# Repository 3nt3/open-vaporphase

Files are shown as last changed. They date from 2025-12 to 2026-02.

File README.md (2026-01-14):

# Open Vaporphase

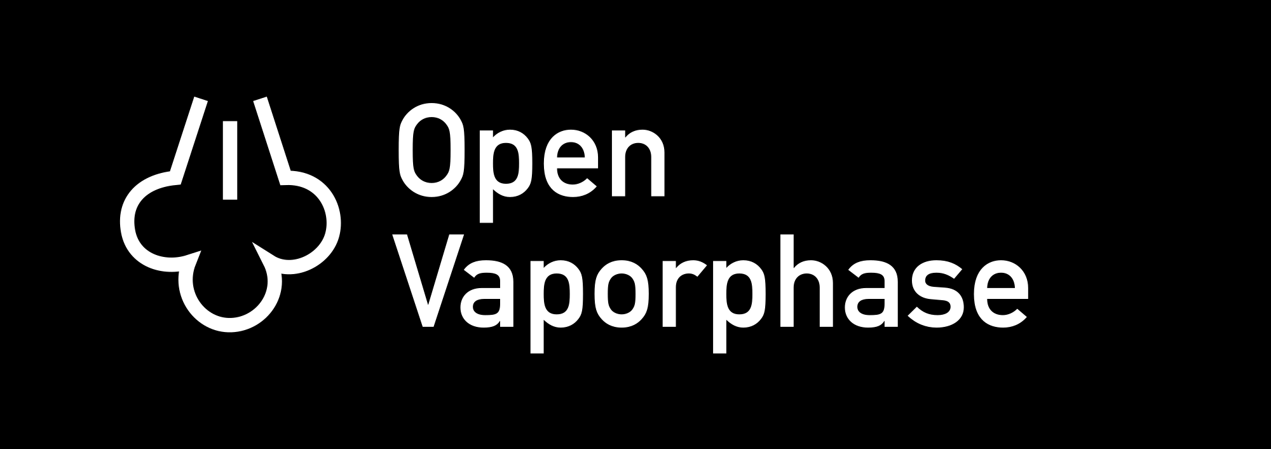
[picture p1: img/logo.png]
Open Vaporphase Logo


# Hardware

## Requirements

- Active cooling
- Ventilation
- Lid switch
- Buzzer to play the Forelle song like a samsung washing machine (required to be configurable to also imitate a rice cooker)

## Safety

We try to follow relevant EU legislature Directive 2006/42/EC (Machinery Directive) as a source of best practices.

### Hazards

- Thermal: High-temperature fluids and surfaces
- Chemical: Vapor phase fluids (PFPE, Galden, etc.)
- Electrical

### Ideas

- Heater control fails OFF
- Loss of sensor input disables heating
- Prevention of runoff heating when liquid is missing
- Lid-open condition prevents heating
- Manual emergency stop immediately removes power

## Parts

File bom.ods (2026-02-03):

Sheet: Sheet1
Open Vaporphase BOM
Qty | Description | Supplier | Part Number | Individual Cost | Total Cost | Note | Kilometerstein | Status
4.00 | TT-PT1000B-2050-11-AUNITEWA TEMPERATURE SENSORS-Sensor Temperatur | TME | TT-PT1000B-2050-11 | 2.78 € | 11.12 € |  | 1.00 | To-Do
2.00 | RS PRO Heizelement Heizpatrone 500 W / 220 V ac, Ø 16 mm, Länge 150mm | RS-Components | 860-6993 | 32.45 € | 64.90 € |  | 1.00 | To-Do
1.00 | TE Connectivity Mini Puck SSRMP Tafelmontage Halbleiterrelais mit Nulldurchgang, 1-poliger Schließer 280 V / 25 A | RS-Components | 204-7642 | 18.04 € | 18.04 € |  | 1.00 | To-Do
1.00 | RS PRO DIN-Schienen Netzteil Schaltnetzteile 5V dc / 2.4A 12W 90 → 264V ac | RS-Components | 225-9899 | 16.27 € | 16.27 € |  | 2.00 | To-Do
1.00 | 30×30 Bosch Rexroth compatible aluminium extrusion and connectors | Motedis |  | 60.00 € | 60.00 € | TODO: actual itemized list | 2.00 | To-Do
1.00 | METRO Professional GN-Behälter 1/3, 200 mm, Edelstahl 18/10 | Metro | AAA0046067392 | 16.65 € | 16.65 € |  | 1.00 | Done
1.00 | Custom Machined Heatsink | JLCCNC |  | 45.00 € | 45.00 € |  | 1.00 | Ordered
1.00 | Cooper Pipe Ø 15 mm, l = 2000 mm | Bauhaus | 27689806 | 21.00 € | 21.00 € |  | 1.00 | To-Do
2.00 | Flow sensors | Amazon | https://www.amazon.de/ARCELI-Wasserdurchfluss-Wassersteuerung-Wasserdurchflussschalter-Durchflussmesser/dp/B07MY24YFX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 | 8.00 € | 16.00 € | Can’t find any affordable ones from reputable suppliers | 2.00 | To-Do
1.00 | 480×320px IPS Display with ILI9486 controller | Amazon | https://www.amazon.de/Binghe-5-Zoll-TFT-Farbmodul-SD-Kartensockel-Reichhaltige-Kompatibel/dp/B0DS1QDDK1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 | 17.00 € | 17.00 € |  | 1.00 | To-Do
1.00 | ESP32-S3-WROOM-1-N16 | Digikey |  |  | 0.00 € | Lol | 1.00 | To-Do
1.00 | Misc | Digikey |  |  | 0.00 € |  | 1.00 | To-Do
1.00 | High Temperature Silicone RUBAAAAH: TFC Trollfactory Silkon Kautschunk Typ 3 | Trollfactory | https://trollfactory.de/Produkte/Silikon-Kautschuk/Verarbeitungszeit/sehr-schnell-5-Min/TFC4020/TFC-Troll-Factory-Silikon-Kautschuk-Typ-3-HB-Zinnguss-hitzebes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 | 19.90 € | 19.90 € |  | 1.00 | To-Do
1.00 | Copper Sheet Metal 2 mm | ProKilo | N/A | 20.00 € | 20.00 € |  | 1.00 | To-Do
1.00 | Glass plate | ??? | ??? | ??? | #VALUE! |  | 1.00 | To-Do
1.00 | Nutri Score: LUFT |  |  | 40.00 € | 40.00 € |  | 2.00 | To-Do
1.00 | Galdne |  |  | 80.00 | 80.00 € |  | 1.60 | To-Do
1.00 | Aluminium Barstock 30×5 | ProKilo | N/A | 7.70 € | 7.70 € |  | 1.00 | To-Do
 |  |  |  | Total v0.1 | 241.31 €
 |  |  |  | Total Cost | 453.58 €

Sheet: Sheet2
Qty | Description | Supplier | Part Number | Individual Cost | Total Cost | Note | Kilometerstein | Status
4.00 | RS PRO PT100 Chip RTD-Sensor Platin Ø 2mm x 5mm, -50°C → +500°C | RS-Components | 611-7801 | 4.13 € | 16.52 € |  | 1.00 | Done
2.00 | RS PRO Heizelement Heizpatrone 500 W / 220 V ac, Ø 16 mm, Länge 150mm | RS-Components | 860-6993 | 32.45 € | 64.90 € |  | 1.00 | Done
1.00 | TE Connectivity Mini Puck SSRMP Tafelmontage Halbleiterrelais mit Nulldurchgang, 1-poliger Schließer 280 V / 25 A | RS-Components | 204-7642 | 18.04 € | 18.04 € |  | 1.00 | Done
1.00 | RS PRO DIN-Schienen Netzteil Schaltnetzteile 5V dc / 2.4A 12W 90 → 264V ac | RS-Components | 225-9899 | 16.27 € | 16.27 € |  | 2.00 | To-Do
1.00 | 30×30 Bosch Rexroth compatible aluminium extrusion and connectors | Motedis |  | 60.00 € | 60.00 € | TODO: actual itemized list | 2.00 | To-Do
1.00 | METRO Professional GN-Behälter 1/3, 200 mm, Edelstahl 18/10 | Metro | AAA0046067392 | 16.65 € | 16.65 € |  | 1.00 | Done
1.00 | Custom Machined Heatsink | JLCCNC |  | 45.00 € | 45.00 € |  | 1.00 | Ordered
1.00 | Cooper Pipe Ø 15 mm, l = 2000 mm | Bauhaus | 27689806 | 21.00 € | 21.00 € |  | 1.00 | To-Do
2.00 | Flow sensors | Amazon | https://www.amazon.de/ARCELI-Wasserdurchfluss-Wassersteuerung-Wasserdurchflussschalter-Durchflussmesser/dp/B07MY24YFX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 | 8.00 € | 16.00 € | Can’t find any affordable ones from reputable suppliers | 2.00 | To-Do
1.00 | 480×320px IPS Display with ILI9486 controller | Amazon | https://www.amazon.de/Binghe-5-Zoll-TFT-Farbmodul-SD-Kartensockel-Reichhaltige-Kompatibel/dp/B0DS1QDDK1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 | 17.00 € | 17.00 € |  | 1.00 | To-Do
1.00 | ESP32-S3-WROOM-1-N16 | Digikey |  |  | 0.00 € | Lol | 1.00 | To-Do
1.00 | Misc | Digikey |  |  | 0.00 € |  | 1.00 | To-Do
1.00 | High Temperature Silicone RUBAAAAH: TFC Trollfactory Silkon Kautschunk Typ 3 | Trollfactory | https://trollfactory.de/Produkte/Silikon-Kautschuk/Verarbeitungszeit/sehr-schnell-5-Min/TFC4020/TFC-Troll-Factory-Silikon-Kautschuk-Typ-3-HB-Zinnguss-hitzebes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 | 19.90 € | 19.90 € |  | 1.00 | To-Do
1.00 | Copper Sheet Metal 2 mm | ProKilo | N/A | 20.00 € | 20.00 € |  | 1.00 | To-Do
1.00 | Glass plate | ??? | ??? | ??? | #VALUE! |  | 1.00 | To-Do
1.00 | Nutri Score: LUFT |  |  | 40.00 € | 40.00 € |  | 2.00 | To-Do
1.00 | Galdne |  |  | 80.00 | 80.00 € |  | 1.60 | To-Do
1.00 | Aluminium Barstock 30×5 | ProKilo | N/A | 7.70 € | 7.70 € |  | 1.00 | To-Do

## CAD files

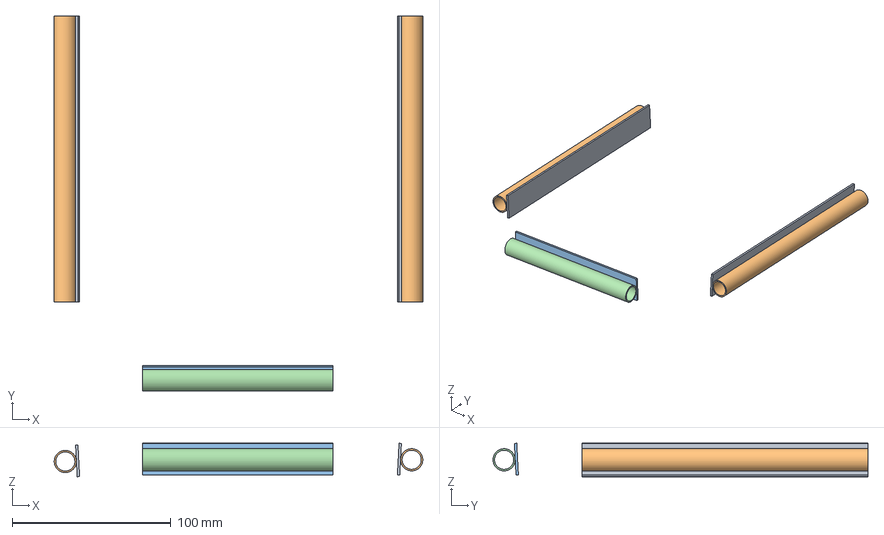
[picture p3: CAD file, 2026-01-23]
cad/open-vaporphase.FCStd
232.0 x 236.0 x 21.1 mm
spreader x 2
pipe x 2
spreader001
pipe001

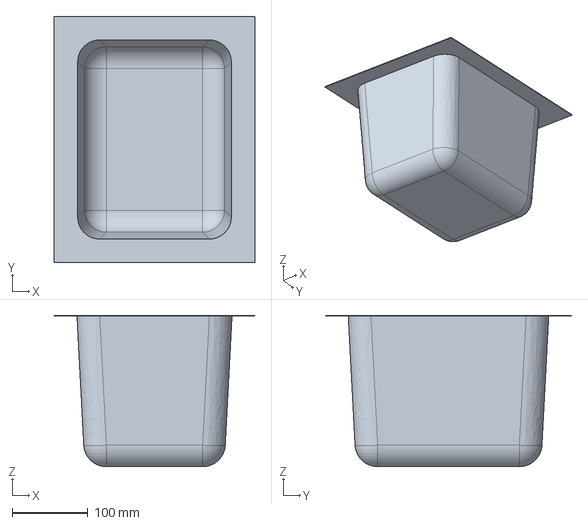
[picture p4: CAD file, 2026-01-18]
cad/res/1-2 gastronorm.FCStd
265.0 x 325.0 x 200.0 mm

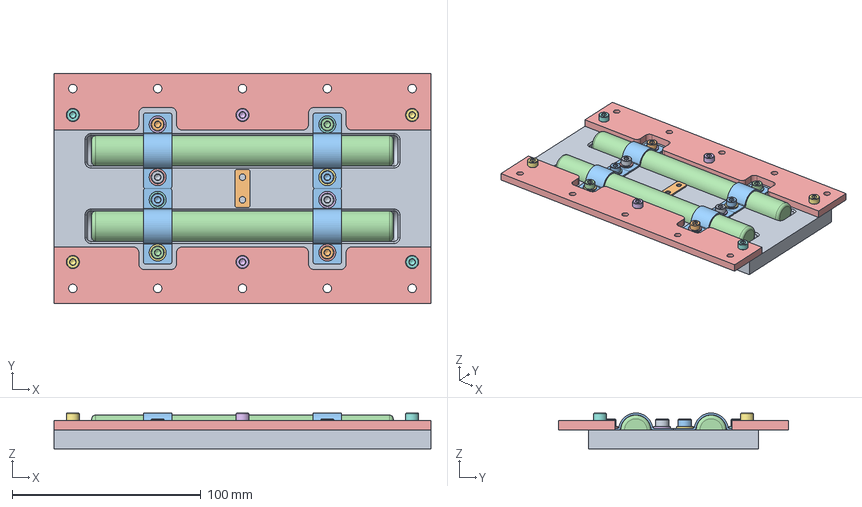
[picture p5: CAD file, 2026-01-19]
cad/16mm heater block.FCStd
200.0 x 122.0 x 19.1 mm
16mm block v2
thermocouple clamp
clamp x 4
16mm heater x 2
M4-Washer007
M4-Washer006
M4-Washer
M4-Washer001
M4x8-Screw096
M4x8-Screw095
M4x8-Screw092
M4x8-Screw
M4-Washer002
M4-Washer003
M4-Washer004
M4-Washer005
M4x8-Screw093
M4x8-Screw094
M4x8-Screw097
M4x8-Screw098
clamp thing x 2
M4x12-Screw002 x 2
M4x12-Screw x 2
M4x12-Screw003 x 2

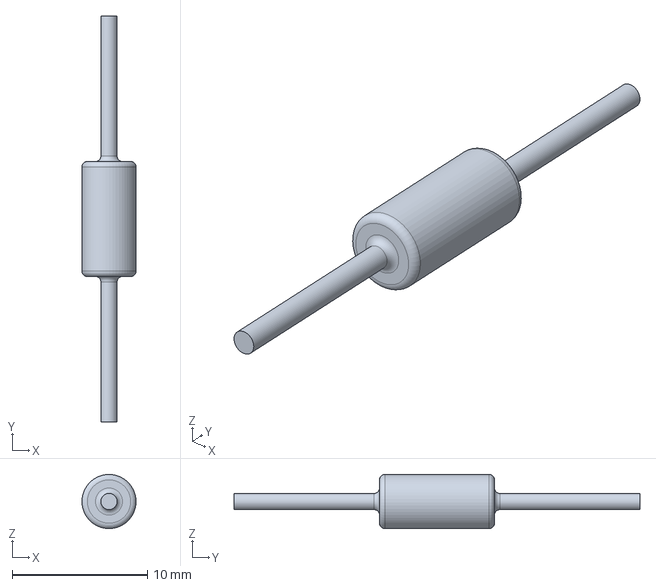
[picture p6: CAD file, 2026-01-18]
cad/res/797-6030 temperature fuse.FCStd
4.00 x 30.0 x 4.00 mm

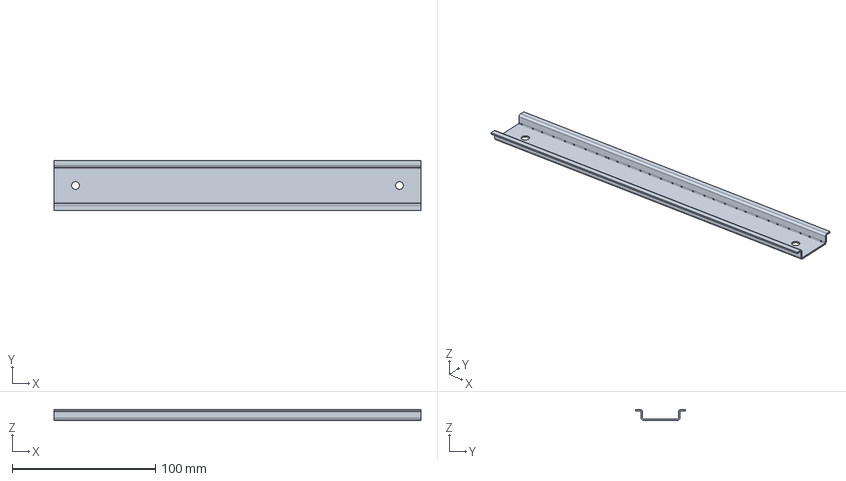
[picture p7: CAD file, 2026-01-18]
cad/res/din rail.FCStd
256.0 x 35.0 x 7.50 mm

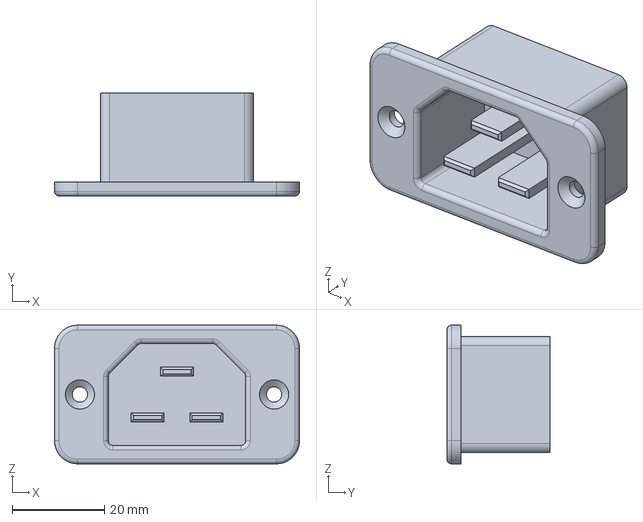
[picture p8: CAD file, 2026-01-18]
cad/res/866-2640 iec plug.FCStd
53.0 x 22.3 x 30.0 mm

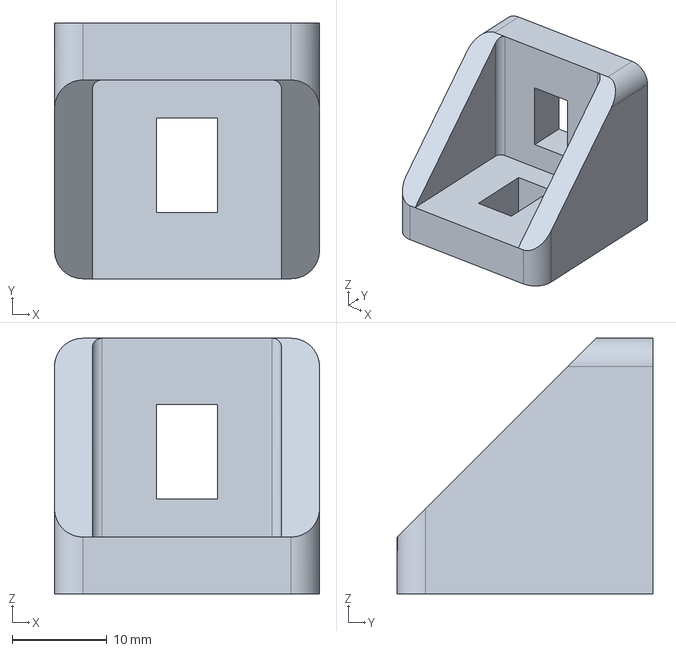
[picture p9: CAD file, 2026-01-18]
cad/res/236-7194 3030 90deg m6.FCStd
28.0 x 27.0 x 27.0 mm

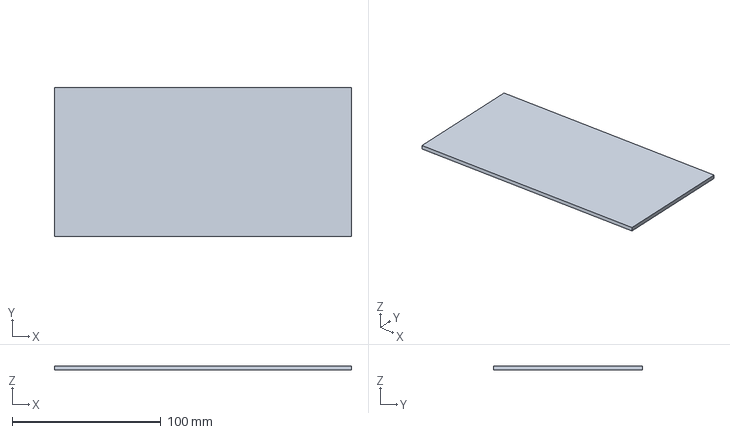
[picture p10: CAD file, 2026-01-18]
cad/res/790-4833 heating pad.FCStd
200.0 x 100.0 x 3.00 mm

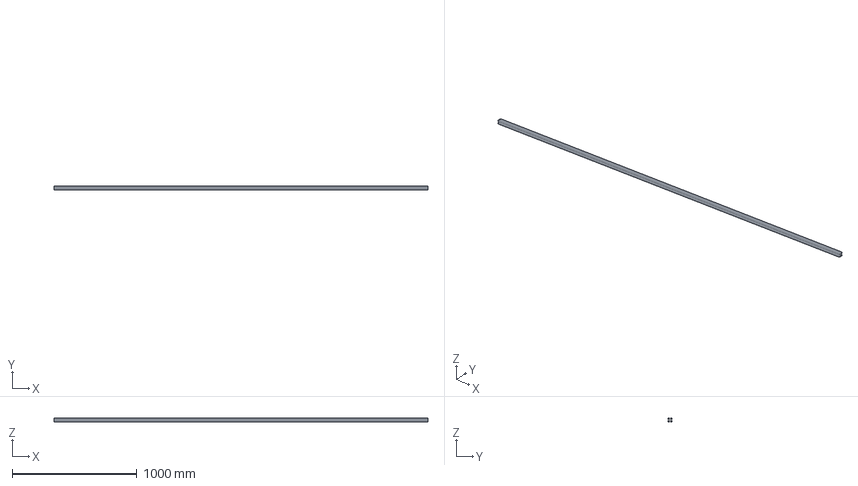
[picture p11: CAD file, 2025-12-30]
cad/res/176240558-3-3842990720_3000/3842990720_3000.stp
3000.0 x 30.0 x 30.0 mm

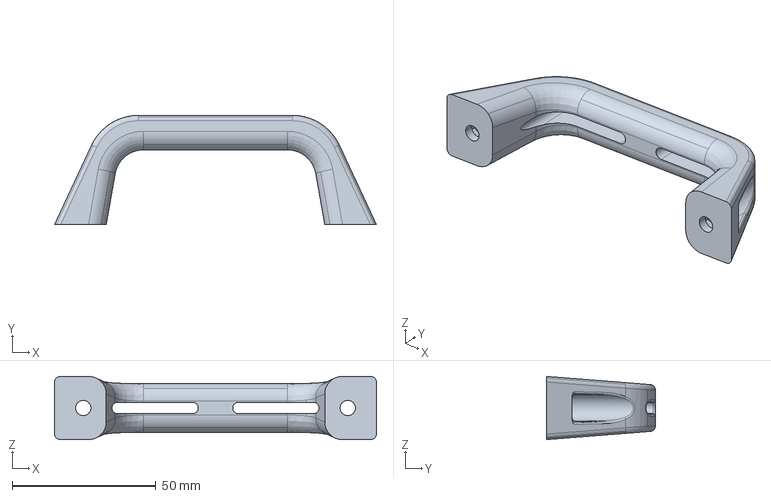
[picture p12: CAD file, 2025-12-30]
cad/res/456589.stp
112.0 x 38.0 x 22.0 mm

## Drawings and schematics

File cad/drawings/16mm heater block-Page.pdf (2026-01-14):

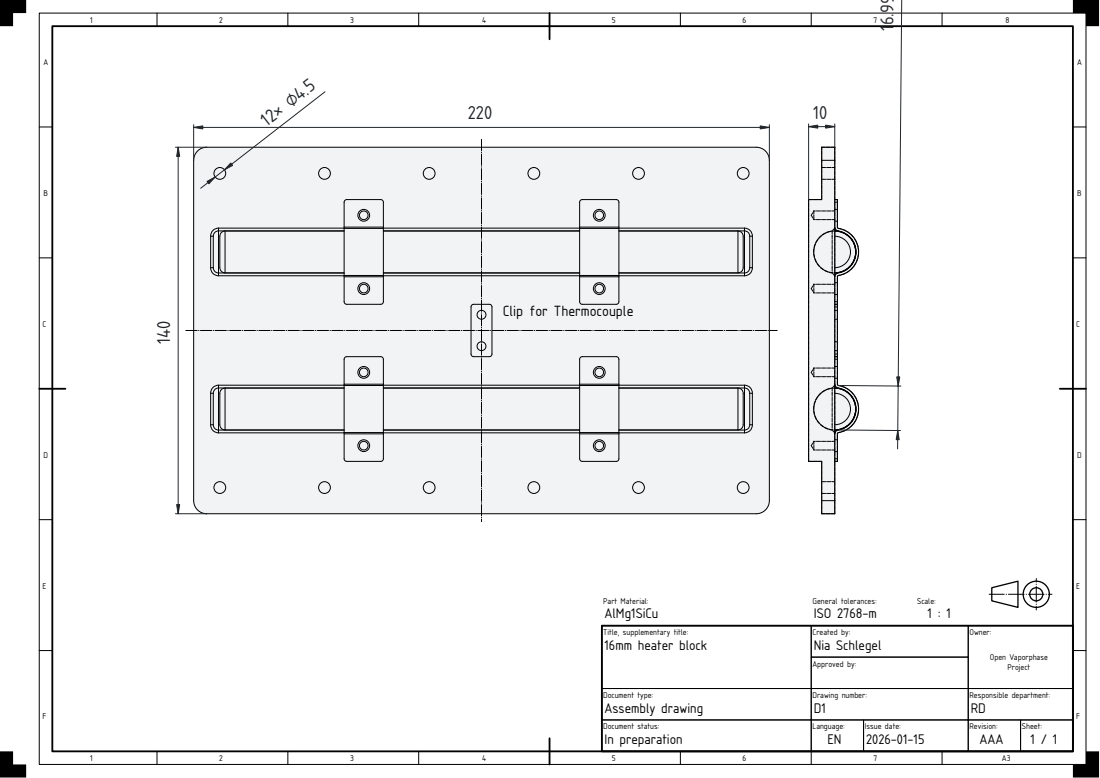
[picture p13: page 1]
Approved by:; Created by:; Part Material:; General tolerances:; Scale:; Open Vaporphase; Nia Schlegel; AlMg1SiCu; ISO 2768-m

Clip for Thermocouple

Title, supplementary title:
16mm heater block

Document type: Assembly drawing | Drawing number: D1 | Responsible department: RD

Document status: In preparation | Language: EN | Issue date: 2026-01-15 | Revision: AAA | Sheet: 1 / 1

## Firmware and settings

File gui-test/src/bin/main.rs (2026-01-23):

#![no_std]
#![no_main]
#![deny(
    clippy::mem_forget,
    reason = "mem::forget is generally not safe to do with esp_hal types, especially those \
    holding buffers for the duration of a data transfer."
)]
#![deny(clippy::large_stack_frames)]

use defmt::info;
use embassy_executor::Spawner;
use embassy_time::{Duration, Timer};
use esp_hal::clock::CpuClock;
use esp_hal::timer::timg::TimerGroup;
use {esp_backtrace as _, esp_println as _};

extern crate alloc;

// This creates a default app-descriptor required by the esp-idf bootloader.
// For more information see: <https://docs.espressif.com/projects/esp-idf/en/stable/esp32/api-reference/system/app_image_format.html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>
esp_bootloader_esp_idf::esp_app_desc!();

#[allow(
    clippy::large_stack_frames,
    reason = "it's not unusual to allocate larger buffers etc. in main"
)]
#[esp_rtos::main]
async fn main(spawner: Spawner) -> ! {
    // generator version: 1.1.0

    let config = esp_hal::Config::default().with_cpu_clock(CpuClock::max());
    let peripherals = esp_hal::init(config);

    esp_alloc::heap_allocator!(#[esp_hal::ram(reclaimed)] size: 73744);

    let timg0 = TimerGroup::new(peripherals.TIMG0);
    esp_rtos::start(timg0.timer0);

    info!("Embassy initialized!");

    let radio_init = esp_radio::init().expect("Failed to initialize Wi-Fi/BLE controller");
    let (mut _wifi_controller, _interfaces) =
        esp_radio::wifi::new(&radio_init, peripherals.WIFI, Default::default())
            .expect("Failed to initialize Wi-Fi controller");

    // TODO: Spawn some tasks
    let _ = spawner;

    loop {
        info!("Hello world!");
        Timer::after(Duration::from_secs(1)).await;
    }

    // for inspiration have a look at the examples at https://github.com/esp-rs/esp-hal/tree/esp-hal-v~1.0/examples
}

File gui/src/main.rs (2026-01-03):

use slint::{ModelRc, SharedVector, Timer, format};
use std::time::Duration;

slint::include_modules!();

fn main() {
    let main_window = MainWindow::new().unwrap();

    let cycle_duration = Duration::from_secs(15 * 60); // 15 minutes
    let start_time = std::time::Instant::now();
    let total_duration = cycle_duration;

    let mut n_past_temps = 0;
    let mut past_temperatures: [f32; 20] = [0.0; 20];

    // Update timer
    let main_window_weak = main_window.as_weak();
    let timer = Timer::default();
    timer.start(
        slint::TimerMode::Repeated,
        Duration::from_millis(100), // Update 10x per second
        move || {
            let main_window = main_window_weak.unwrap();
            let elapsed = start_time.elapsed();

            if elapsed >= total_duration {
                main_window.set_time_remaining("00:00".into());
                main_window.set_is_running(false);

                return;
            }

            let remaining = total_duration - elapsed;
            let remaining_str = format!(
                "{:02}:{:02}",
                remaining.as_secs() / 60,
                remaining.as_secs() % 60
            );

            main_window.set_time_remaining(remaining_str.into());

            // random temp between 170 and 180
            let random_temp: f32 = 170.0 + rand::random::<f32>() * 10.0;
            main_window.set_temperature(format!("{:.1}", random_temp));

            // Update past temperatures
            if n_past_temps < 20 {
                n_past_temps += 1;
            }
            past_temperatures.rotate_right(1);
            past_temperatures[0] = random_temp;

            main_window.set_past_temperatures(past_temperatures.into());
        },
    );

    main_window.run().unwrap();
}

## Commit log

2025-12-30 cad wip
    [3842990720_3000.stp, 456589.stp, 866-2640 iec plug.FCStd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]
2026-01-01 make frame more complete
    [open-vaporphase.FCStd]
2026-01-02 add temperature sensor
    [open-vaporphase.FCStd]
2026-01-02 add thermal fuse
    [open-vaporphase.FCStd]
2026-01-02 add thermal fuse cad
    [797-6030 temperature fuse.FCStd, open-vaporphase.FCStd]
2026-01-02 make frame larger to fit electrical compartment
    [open-vaporphase.FCStd]
2026-01-02 tidy cad
    [797-6030 temperature fuse.FCStd, 866-2640 iec plug.FCStd, open-vaporphase.FCStd]
2026-01-02 add din rail
    [din rail.FCStd, open-vaporphase.FCStd]
2026-01-02 add basic things to schematic
    [open-vaporphase.FCStd, open-vaporphase.kicad_pcb, open-vaporphase.kicad_sch]
2026-01-02 schematic wip
    [open-vaporphase.kicad_sch]
2026-01-03 add connectors for aluminum extrusion
    [236-7194 3030 90deg m6.FCStd, 790-4833 heating pad.FCStd, open-vaporphase.FCStd]
2026-01-03 add heatsink and also a lot of other stuff
    [16mm heater block.FCStd, 236-7194 3030 90deg m6.FCStd, 790-4833 heating pad.FCStd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]
2026-01-05 idk just what i currently have
    [open-vaporphase.FCStd]
2026-01-09 add bom
    [16mm heater block.FCStd, 236-7194 3030 90deg m6.FCStd, 790-4833 heating pad.FCStd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]
2026-01-10 remove bom section
2026-01-14 change heater block design for 1/2 GN container
    [16mm heater block-Part01416mm block v2.step, 16mm heater block-Part01416mm block v2.stl, 16mm heater block.FCStd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]
2026-01-15 change heating elements to 500w/160mm and remove exports
    [16mm heater block-Part01416mm block v2.step, 16mm heater block-Part01416mm block v2.stl, 16mm heater block.FCStd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]
2026-01-15 add wing-y brackets as extra components
    [16mm heater block.FCStd]
2026-01-15 saving before changing container size
    [16mm heater block.FCStd, bom.ods, open-vaporphase.FCStd]
2026-01-16 add 1-2 gastronorm
    [1-2 gastronorm.FCStd, open-vaporphase.FCStd]
2026-01-16 change heatsink to fit
    [1-2 gastronorm.FCStd, 16mm heater block.FCStd, open-vaporphase.FCStd]
2026-01-18 add waterblocks
    [1-2 gastronorm.FCStd, 16mm heater block.FCStd, 236-7194 3030 90deg m6.FCStd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]
2026-01-19 make heater narrower to fit
    [16mm heater block.FCStd, open-vaporphase.FCStd]
2026-01-19 clean up hierarchy
    [16mm heater block.FCStd, open-vaporphase.FCStd]
2026-01-23 add holes for thermocouple clamp
    [16mm heater block-everything16mm block v2.step, open-vaporphase.FCStd]
2026-01-23 remove step file
    [16mm heater block-everything16mm block v2.step]
2026-01-26 update bom
    [bom.ods]
2026-02-03 mark rs order as done
    [bom.ods]
